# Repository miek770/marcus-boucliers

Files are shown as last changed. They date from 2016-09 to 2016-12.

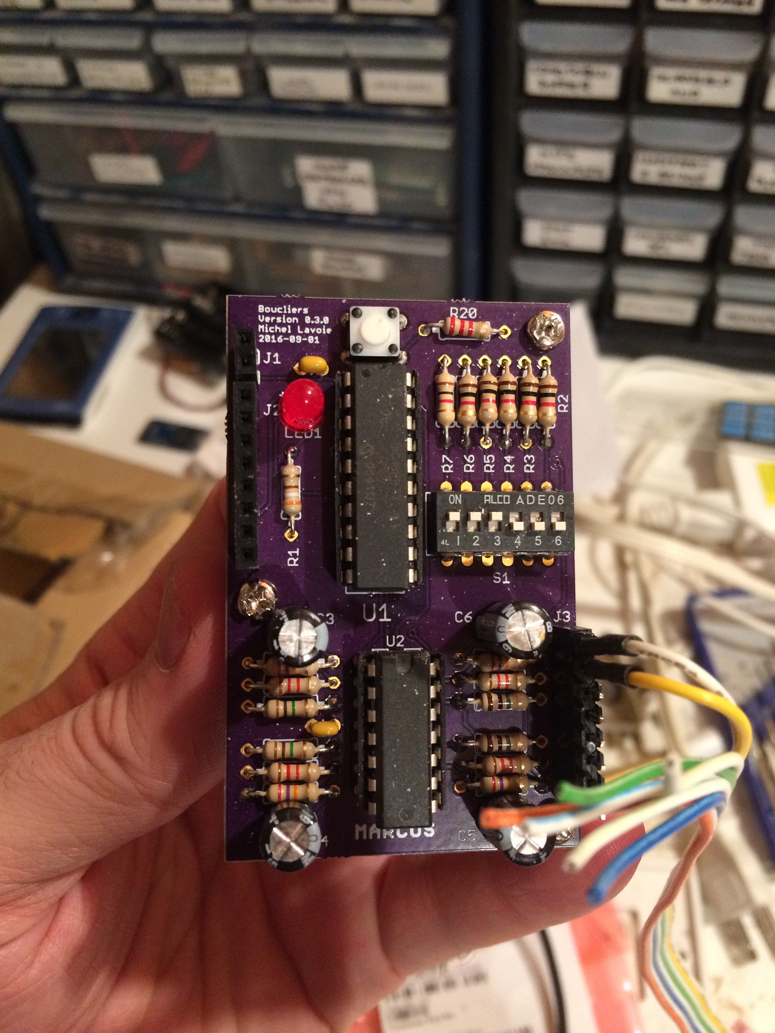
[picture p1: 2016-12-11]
media/Result.jpeg

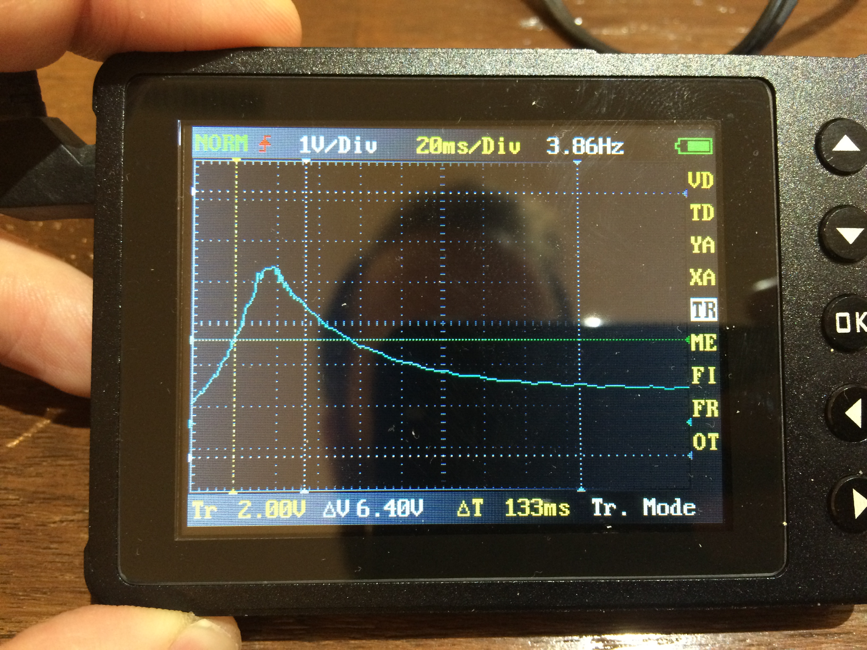
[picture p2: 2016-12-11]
media/Hit detection.jpg

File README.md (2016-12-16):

# Marcus - Circuit standard des boucliers

## 1. Améliorations pour la prochaine version

1. Ajouter des points de tests pour le raccordement facile d'un oscilloscope;
2. Ajouter un bornier de programmation pour le PIC avec le PICkit2;
3. Inverser la masse et le 5V sur le bouton de réinitialisation, et s'assurer que tous les signaux sont raccordés;
4. Inverser les interrupteurs DIP pour la programmation des points de vie;
5. À partir de maintenant, toujours indiquer les alimentations sur la couche de texte. Sur les autres borniers, indiquer la borne 1 et les masses.

### 1.1 Améliorations optionnelles, à considérer

1. Peut-être ajouter une LED verte pour indiquer que le robot est encore en vie, quitte à mettre un mini-bornier pour un cavalier. Mais c'est vraiment optionnel, à valider;
2. Remplacer les sorties digitales non-essentielles (information) par un port de communication I2C;
3. Faire un format de PCB pouvant être empilé avec le BBB.

## 2. Caractéristiques techniques

- Tension d'alimentation
  - Minimal : 5Vcc
  - Maximal : 6Vcc
- Niveau logique
  - 0-5 Vcc (TTL)
- Temps de réaction
  - À compléter
- Fréquence : 4MHz

## 3. Borniers d'interface

- TB0 : Alimentation
  - 1. Gnd
  - 2. 5V
- TB1 : Interface contrôleur
  - 1. Mort
  - 2. Bouclier 1
  - 3. Bouclier 2
  - 4. Bouclier 3
  - 5. Bouclier 4
  - 6. Réinitialise
  - 7. RB7
  - 8. Gnd
- TB2 : Interface boucliers
  - 1. Bouclier 1
  - 2. Gnd
  - 3. Bouclier 2
  - 4. Gnd
  - 5. Bouclier 3
  - 6. Gnd
  - 7. Bouclier 4
  - 8. Gnd

### 3.1 TB0 – Alimentation

Ce bornier sert à fournir une alimentation régulée à l'externe à une tension entre 5 et 6 VCC. Il n'y a aucun régulateur de tension ni condensateur régulateur dans le circuit standard des boucliers. La masse doit être isolée des composants de puissance afin d'éviter de perturber le fonctionnement des composants sensibles du circuit.

### 3.2 TB1 – Interface contrôleur

L'interface contrôleur sert à communiquer de l'information sur l'état des boucliers au contrôleur principal, et à recevoir des commandes de réinitialisation une fois que les données ont bien été communiquées.

#### 3.2.1 Sorties

Les bornes 3 à 7, c'est-à-dire « Mort », « Bouclier 1 », « Bouclier 2 », « Bouclier 3 » et « Bouclier 4 » servent à communiquer l'état des boucliers, ainsi que le statut de mort (voir section 4). La sortie « Mort » est normalement à 0 et passe à 1 (voir section 2) lorsque les points de vies ont été épuisés (voir section 4). Après que la sortie soit passée à 1, une réinitialisation manuelle […] ou une coupure de l'alimentation V+ est requise afin de remettre le compteur de vies à sa valeur initiale et remettre la sortie de mort à 0. Les sorties « Bouclier 1 », « Bouclier 2 », « Bouclier 3 » et « Bouclier 4 » sont normalement à 0 et passent à 1 (voir section 2) lorsqu'un impact réussi […] est détecté sur le bouclier correspondant. La sortie en question est maintenue à 1 jusqu'à la prochaine réinitialisation logicielle (voir section 3.2.2). Il est important de noter que la réinitialisation des sorties 4 à 7 n'a aucun effet sur le décompte des impacts, et donc le statut de mort.

#### 3.2.2 Entrée

La borne 8 « Réinitialisation » sert à ramener l'état des sorties 4 à 7 (voir section 3.2.1) à 0, soit leur état au repos. Elle est activée par un 1 logique et n'a aucun effet sur le décompte des impacts ni le statut de mort. Elle est à la disposition du concepteur, pour information, dans le cas où il voudrait inclure l'état des boucliers à sa logique.

#### 3.2.3 RB7

La borne RB7 est actuellement non-utilisée, mais raccordée au signal RB7 du PIC.

### 3.3 TB2 – Interface boucliers

Raccordement des capteurs LDT0 de MEAS (numéro de matériel 0-1002794-1, voir note d'application 111398). Le LM324N alimenté à 0-5V agit comme un redresseur simple alternance, avec un filtre passe-bas ayant une fréquence de coupure de 1/(2*pi*C*R2) = 8Hz, et un gain 1+R2/R1 = 21 à 0Hz. Le signal résultant vers le PIC est donc une belle courbe de détection lissée. Il reste à tester la réponse sur le montage final et à ajuster le gain, au besoin.

Le LDT0 devrait être utilisé comme capteur de vibration, il est donc possible que le gain doive être augmenté considérablement lorsqu'il sera monté sur son bouclier. Une autre solution serait de faire un bouclier flexible et léger et de le fixer sur le capteur lui-même.

En résumé, il reste des tests à faire mais il faudra simplement ajuster les 2 résistances et le condensateur de chaque circuit.

## 4. Points de vie

Les points de vie, à l'état initial, sont définis par la configuration d'un interrupteur DIP à 6 positions alors que le circuit est non-alimenté. Chaque impact détecté abaisse la quantité de points de vie de 1, jusqu'à ce qu'elle atteigne 0. La borne 3 « Mort » passe alors à 1 et le circuit doit être réinitialisé par la méthode décrite en 3.2.1.

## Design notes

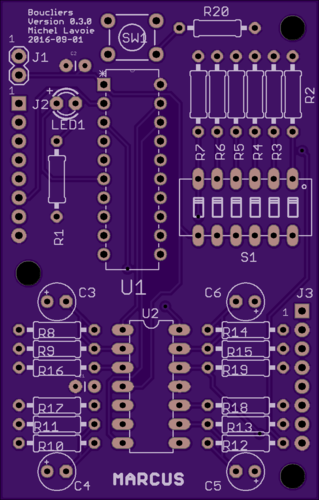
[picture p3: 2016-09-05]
media/Board top.png

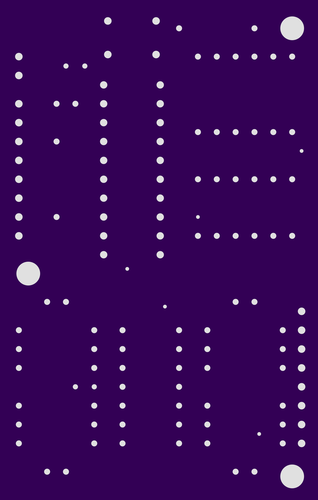
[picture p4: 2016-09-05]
media/Board drilling.png

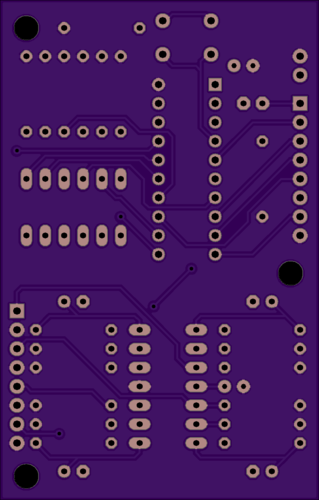
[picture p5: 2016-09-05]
media/Board bottom.png

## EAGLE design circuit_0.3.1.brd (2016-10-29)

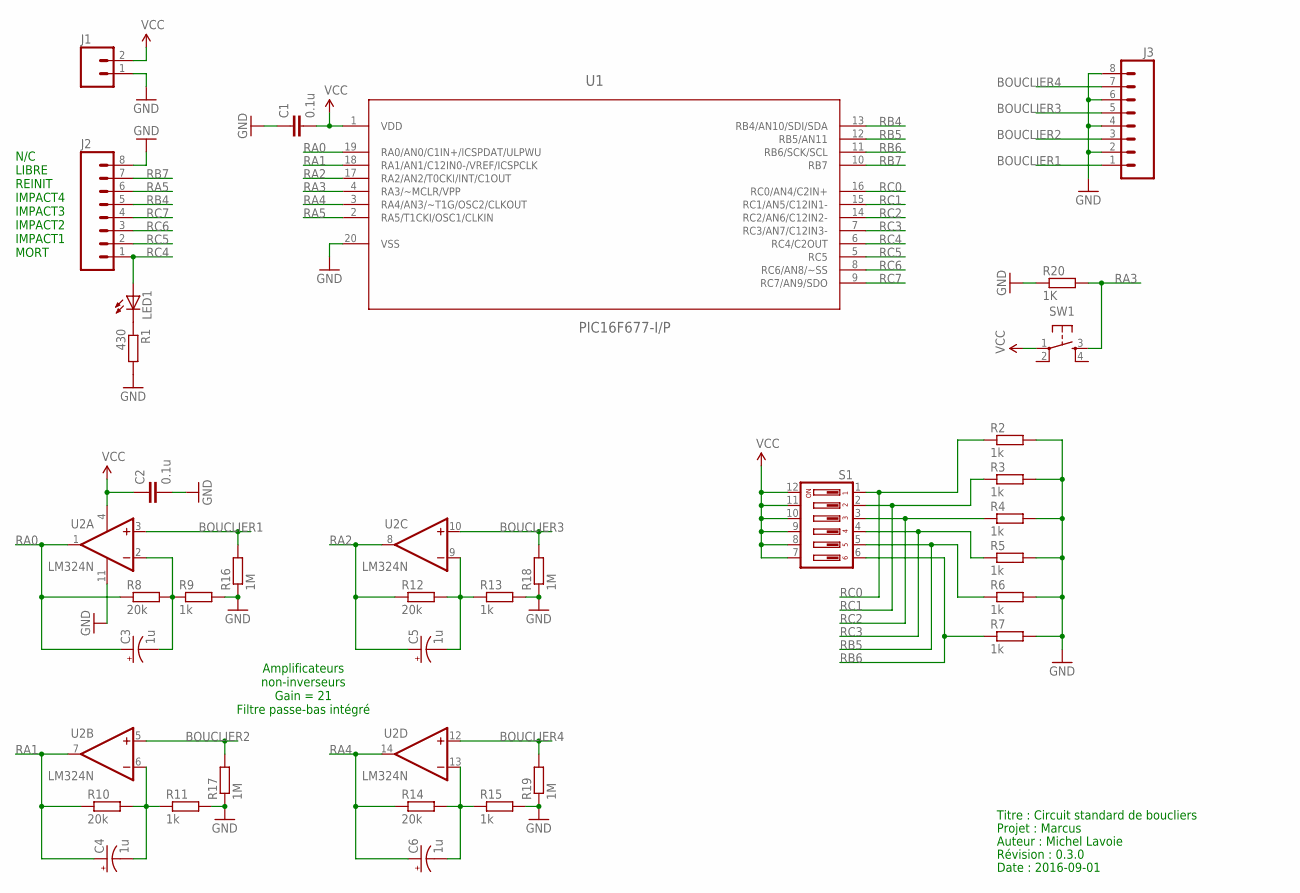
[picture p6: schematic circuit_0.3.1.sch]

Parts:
C1, C2: 0.1u; CAP-PTH-SMALL
C3, C4, C5, C6: 1u; E2,5-5
J1: M02PTH; 1X02
J2, J3: M08NO_SILK; 1X08_PIN1_NO_SILK
LED1: LED3MM
R1: 430; 0207/10
R2, R3, R4, R5, R6, R7, R9, R11, R13, R15: 1k; 0207/10
R8, R10, R12, R14: 20k; 0207/10
R16, R17, R18, R19: 1M; 0207/10
R20: 1K; 0207/10
S1: DIP06YL
SW1: TAC_SWITCHPTH; TACTILE-PTH
U1: PIC16F677-I/P; DIP254P762X533-20
U2: LM324N; DIL14

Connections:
BOUCLIER1: J3.1, R16.2, U2.3 (+IN)
BOUCLIER2: J3.3, R17.2, U2.5 (+IN)
BOUCLIER3: J3.5, R18.2, U2.10 (+IN)
BOUCLIER4: J3.7, R19.2, U2.12 (+IN)
GND: C1.1, C2.2, J1.1, J2.8, J3.2, J3.4, J3.6, J3.8, R1.2, R2.2, R3.2, R4.2, R5.2, R6.2, R7.2, R9.2, R11.2, R13.2, R15.2, R16.1, R17.1, R18.1, R19.1, R20.1, U1.20 (VSS), U2.11 (V-)
unnamed: C4.-, R10.2, R11.1, U2.6 (-IN)
unnamed: LED1.K (C), R1.1
unnamed: C3.-, R8.2, R9.1, U2.2 (-IN)
unnamed: C5.-, R12.2, R13.1, U2.9 (-IN)
unnamed: C6.-, R14.2, R15.1, U2.13 (-IN)
RA0: C3.+, R8.1, U1.19 (RA0/AN0/C1IN+/ICSPDAT/ULPWU), U2.1 (OUT)
RA1: C4.+, R10.1, U1.18 (RA1/AN1/C12IN0-/VREF/ICSPCLK), U2.7 (OUT)
RA2: C5.+, R12.1, U1.17 (RA2/AN2/T0CKI/INT/C1OUT), U2.8 (OUT)
RA3: R20.2, SW1.3, U1.4 (RA3/~MCLR/VPP)
RA4: C6.+, R14.1, U1.3 (RA4/AN3/~T1G/OSC2/CLKOUT), U2.14 (OUT)
RA5: J2.6, U1.2 (RA5/T1CKI/OSC1/CLKIN)
RB4: J2.5, U1.13 (RB4/AN10/SDI/SDA)
RB5: R6.1, S1.5, U1.12 (RB5/AN11)
RB6: R7.1, S1.6, U1.11 (RB6/SCK/SCL)
RB7: J2.7, U1.10 (RB7)
RC0: R2.1, S1.1, U1.16 (RC0/AN4/C2IN+)
RC1: R3.1, S1.2, U1.15 (RC1/AN5/C12IN1-)
RC2: R4.1, S1.3, U1.14 (RC2/AN6/C12IN2-)
RC3: R5.1, S1.4, U1.7 (RC3/AN7/C12IN3-)
RC4: J2.1, LED1.A, U1.6 (RC4/C2OUT)
RC5: J2.2, U1.5 (RC5)
RC6: J2.3, U1.8 (RC6/AN8/~SS)
RC7: J2.4, U1.9 (RC7/AN9/SDO)
VCC: C1.2, C2.1, J1.2, S1.7, S1.8, S1.9, S1.10, S1.11, S1.12, SW1.1, U1.1 (VDD), U2.4 (V+)

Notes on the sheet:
N/C LIBRE REINIT IMPACT4 IMPACT3 IMPACT2 IMPACT1 MORT
Titre : Circuit standard de boucliers
Projet : Marcus
Auteur : Michel Lavoie
Révision : 0.3.0
Date : 2016-09-01
Amplificateurs non-inverseurs Gain = 21 Filtre passe-bas intégré

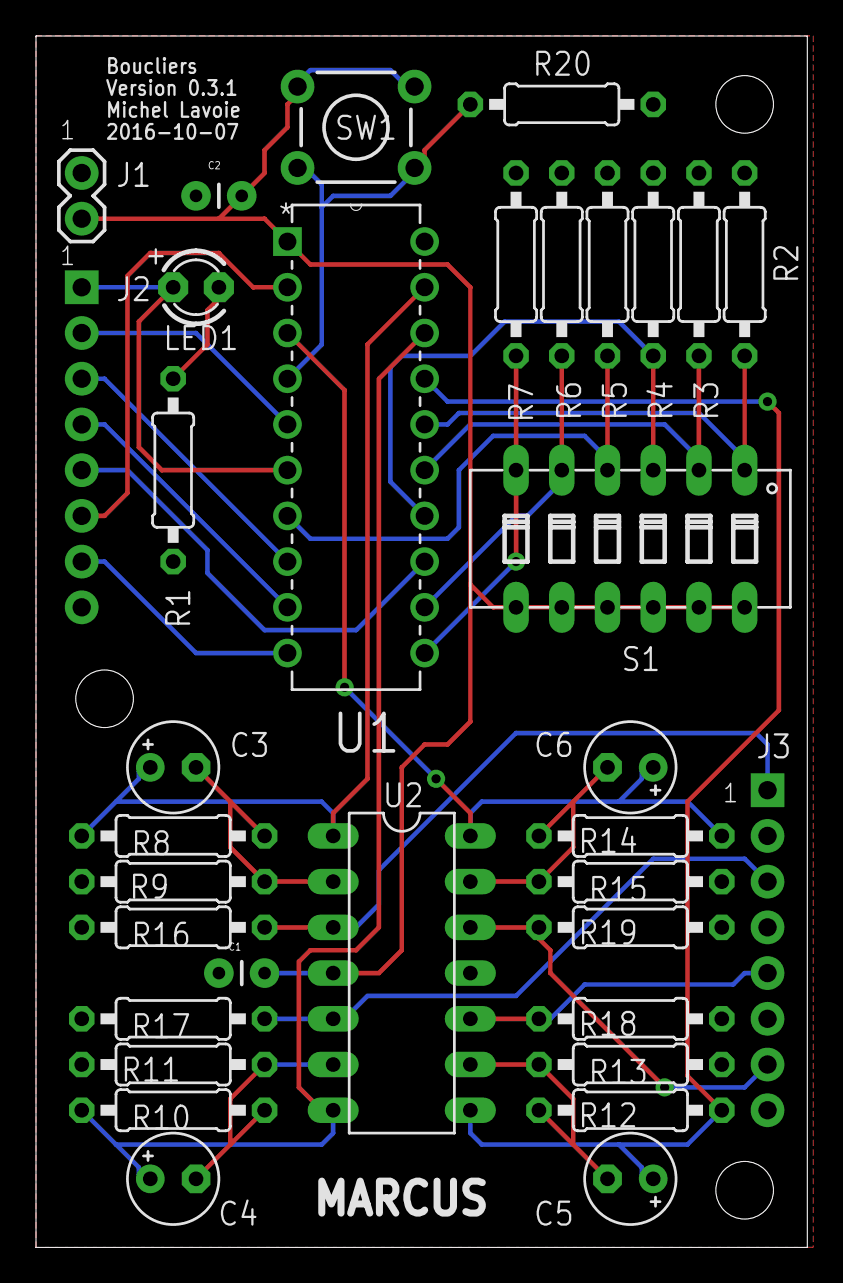
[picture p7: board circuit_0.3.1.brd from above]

Board: 2 copper layers, 42.9 x 67.3 mm, 34 parts (0 on the bottom side), 29 nets.

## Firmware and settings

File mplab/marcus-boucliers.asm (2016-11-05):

; marcus-boucliers.asm

    list    p=16f677            ; list directive to define processor
    #include <p16f677.inc>      ; processor specific variable definitions

    ; Désactive quelques avertissements inutiles
    errorlevel -302
    errorlevel -305

    __CONFIG    _FCMEN_OFF & _IESO_OFF & _BOR_OFF & _CPD_OFF & _CP_OFF & _MCLRE_OFF & _PWRTE_OFF & _WDT_OFF & _INTRC_OSC_NOCLKOUT

; example of using Shared Uninitialized Data Section
INT_VAR     UDATA_SHR
w_temp      RES 1           ; variable used for context saving
status_temp RES 1           ; variable used for context saving
pclath_temp RES 1           ; variable used for context saving

; example of using Uninitialized Data Section
        UDATA   0x20        ; explicit address specified is not required
dc1     RES     1           ; Compteur de délai 1
dc2     RES     1           ; Compteur de délai 2
vies    RES     1           ; Nombre de vies restantes

;============================================================================
RESET_VECTOR CODE   0x0000  ; processor reset vector
;============================================================================
    nop
    goto    depart          ; go to beginning of program

;============================================================================
INT_VECTOR  CODE    0x0004  ; interrupt vector location
;============================================================================
    movwf   w_temp          ; save off current W register contents
    movf    STATUS,w        ; move status register into W register
    movwf   status_temp     ; save off contents of STATUS register
    movf    PCLATH,w        ; move pclath register into w register
    movwf   pclath_temp     ; save off contents of PCLATH register

    btfss   INTCON,RABIF
    goto    quit_interrupt  ; Annule l'interruption si RABIF=0
    banksel PORTA
    btfss   PORTA,5         ; Test RA5  E - Réinitialise (sorties boucliers)
    goto    quit_interrupt
    banksel PORTC
    bcf     PORTC,5         ; RC5  S - Bouclier 1
    bcf     PORTC,6         ; RC6  S - Bouclier 2
    bcf     PORTC,7         ; RC7  S - Bouclier 3
    banksel PORTB
    bcf     PORTB,4         ; RB4  S - Bouclier 4

quit_interrupt:
    bcf     INTCON,RABIF    ; Réinitialise RABIF
    movf    pclath_temp,w   ; retrieve copy of PCLATH register
    movwf   PCLATH          ; restore pre-isr PCLATH register contents
    movf    status_temp,w   ; retrieve copy of STATUS register
    movwf   STATUS          ; restore pre-isr STATUS register contents
    swapf   w_temp,f
    swapf   w_temp,w        ; restore pre-isr W register contents
    retfie                  ; return from interrupt

;============================================================================
MAIN_PROG   CODE            ; program memory
;============================================================================

depart:
; Configuration du port A
    banksel PORTA
    clrf    PORTA
    banksel TRISA
    movlw   b'00111111'     ; | - | - |TRISA5|TRISA4|TRISA3|TRISA2|TRISA1|TRISA0|
    movwf   TRISA
    banksel IOCA
    movlw   b'00100000'     ; | - | - |IOCA5|IOCA4|IOCA3|IOCA2|IOCA1|IOCA0|
    movwf   IOCA
    banksel ANSEL
    clrf    ANSEL
    banksel ANSELH
    clrf    ANSELH

; Configuration du port B
    banksel PORTB
    clrf    PORTB
    banksel TRISB
    movlw   b'11100000'     ; |TRISB7|TRISB6|TRISB5|TRISB4| - | - | - | - |
    movwf   TRISB
    banksel IOCB
    clrf    IOCB

; Configuration du port C
    banksel PORTC
    clrf    PORTC
    banksel TRISC
    movlw   b'00001111'     ; |TRISC7|TRISC6|TRISC5|TRISC4|TRISC3|TRISC2|TRISC1|TRISC0|
    movwf   TRISC

; Allume la LED au démarrage
    banksel PORTC
    bsf     PORTC,4         ; RC4  S - En vie!

; Configuration de la routine d'interruption
    banksel INTCON
    movlw   b'10001000'     ; |GIE|PEIE|T0IE|INTE|RABIE|T0IF|INTF|RABIF|
    movwf   INTCON

; Relève le nombre de vies à utiliser
    call    subCompte_vies

; Boucle principale
    banksel PORTA

main_loop:
    btfsc   PORTA,0         ; Test RA0  E - Bouclier 1
    call    subB1_touche
    btfsc   PORTA,1         ; Test RA1  E - Bouclier 2
    call    subB2_touche
    btfsc   PORTA,2         ; Test RA2  E - Bouclier 3
    call    subB3_touche
    btfsc   PORTA,4         ; Test RA4  E - Bouclier 4
    call    subB4_touche
    goto    main_loop       ; Boucle infinie

;============================================================================
; Routine :        subB1_touche
; Description : Actions à prendre après un impact sur le bouclier 1.
;============================================================================
subB1_touche:
    banksel vies
    decfsz  vies            ; Soustrait une vie
    goto    b1_vivant

    ; Le robot n'a plus de vies
    banksel PORTC
    bcf     PORTC,4         ; RC4  S - Mort
    goto    $               ; Boucle infinie. À changer avec redémarrage.

b1_vivant:
    banksel PORTC
    bsf     PORTC,5         ; RC5  S - Bouclier 1
    call    subDelai_100ms
    banksel PORTA
    return

;============================================================================
; Routine :        subB2_touche
; Description : Actions à prendre après un impact sur le bouclier 2.
;============================================================================
subB2_touche:
    banksel vies
    decfsz  vies            ; Soustrait une vie
    goto    b2_vivant

    ; Le robot n'a plus de vies
    banksel PORTC
    bcf     PORTC,4         ; RC4  S - Mort
    goto    $               ; Boucle infinie. À changer avec redémarrage.

b2_vivant:
    banksel PORTC
    bsf     PORTC,6         ; RC6  S - Bouclier 2
    call    subDelai_100ms
    banksel PORTA
    return

;============================================================================
; Routine :        subB3_touche
; Description : Actions à prendre après un impact sur le bouclier 3.
;============================================================================
subB3_touche:
    banksel vies
    decfsz  vies            ; Soustrait une vie
    goto    b3_vivant

    ; Le robot n'a plus de vies
    banksel PORTC
    bcf     PORTC,4         ; RC4  S - Mort
    goto    $               ; Boucle infinie. À changer avec redémarrage.

b3_vivant:
    banksel PORTC
    bsf     PORTC,7         ; RC7  S - Bouclier 3
    call    subDelai_100ms
    banksel PORTA
    return

;============================================================================
; Routine :        subB4_touche
; Description : Actions à prendre après un impact sur le bouclier 4.
;============================================================================
subB4_touche:
    banksel vies
    decfsz  vies            ; Soustrait une vie
    goto    b4_vivant

    ; Le robot n'a plus de vies
    banksel PORTC
    bcf     PORTC,4         ; RC4  S - Mort
    goto    $               ; Boucle infinie. À changer avec redémarrage.
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

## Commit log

2016-09-05 Initialisation, après commande du PCB.
    [circuit_0.3.0.brd, circuit_0.3.0.sch, circuit_R1.brd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]
2016-09-05 Effacé les révision précédentes.
    [circuit_R1.brd, circuit_R1.sch, circuit_R1a.brd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]
2016-09-05 Effacé BOM qui n'était pas à jour de toute façon.
2016-10-29 Circuit 0.3.1 fonctionnel avec code PIC.
    [circuit_0.3.1.brd, circuit_0.3.1.sch]
2016-10-29 Nettoyé le code, effacé la version 0.3.0.
    [circuit_0.3.0.brd, circuit_0.3.0.sch]
2016-10-30 Correction des masses (Gnd).

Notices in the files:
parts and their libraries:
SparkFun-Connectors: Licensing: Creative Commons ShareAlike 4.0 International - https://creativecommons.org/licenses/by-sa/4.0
